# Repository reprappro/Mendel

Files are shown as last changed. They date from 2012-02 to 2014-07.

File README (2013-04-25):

This is repository the RepRapPro Tricolour and Mono Mendel.

Files for the latest extruder drive may be found here:

https://github.com/reprappro/Extruder-drive

Files for the original RepRapPro Mendel maybe found at the following address:

https://github.com/reprappro/Mendel/archive/Mendel-V1.0.zip

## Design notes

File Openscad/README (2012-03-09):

These OpenSCAD files have names that tell you how many copies to print.

Ones that end in readme make multiple objects - read the comments at their head
to find out what to print.

Ones that have neither ending are library files for the others.

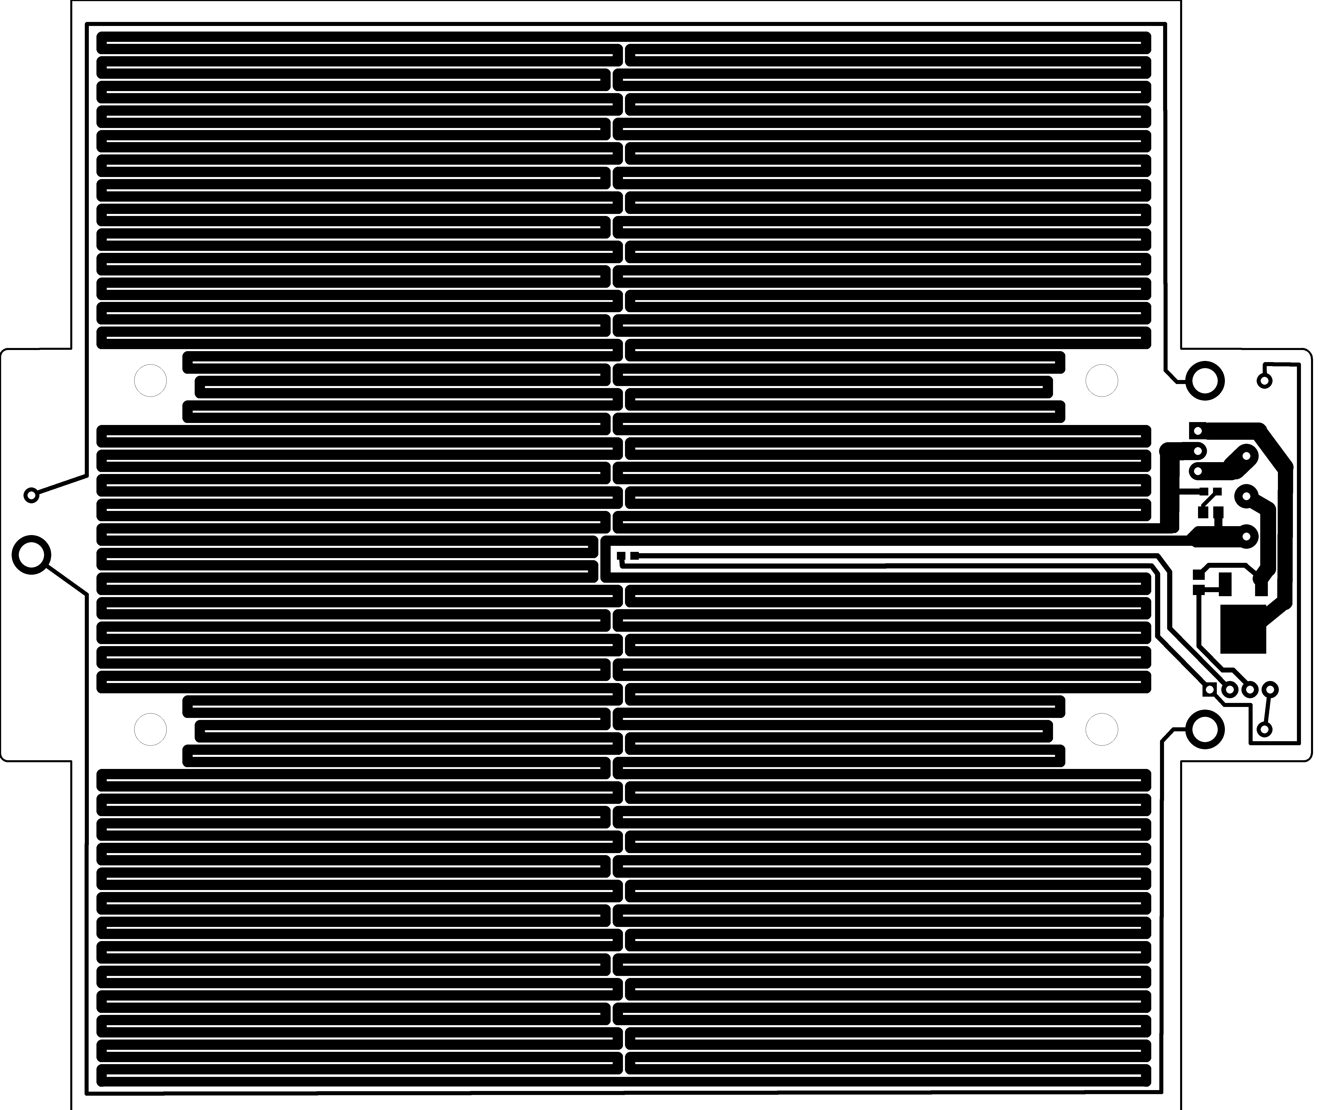
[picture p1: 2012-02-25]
gEDA/Heatbed/heatbed.png

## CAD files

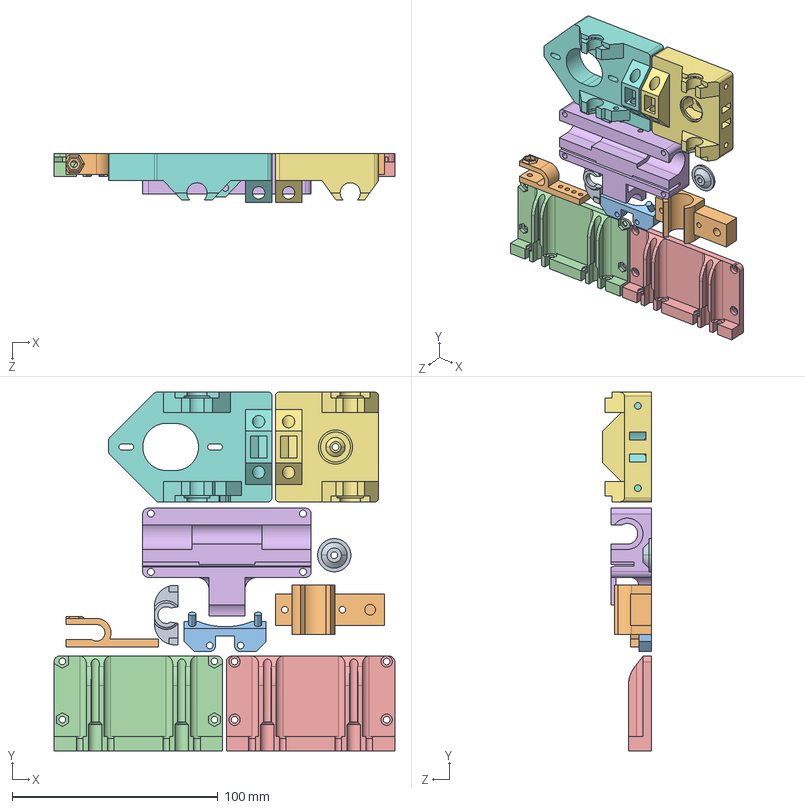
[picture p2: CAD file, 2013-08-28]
SW/Step/RP-assembly.STEP
165.8 x 174.6 x 23.6 mm
Belt Guide
EndStop-Holder
Fan Holder
nozzle-mount-front
nozzle-mount-rear
x-carriage
x-end-idler
x-end-motor
x-idler-cover
Y-Bearing-Holder

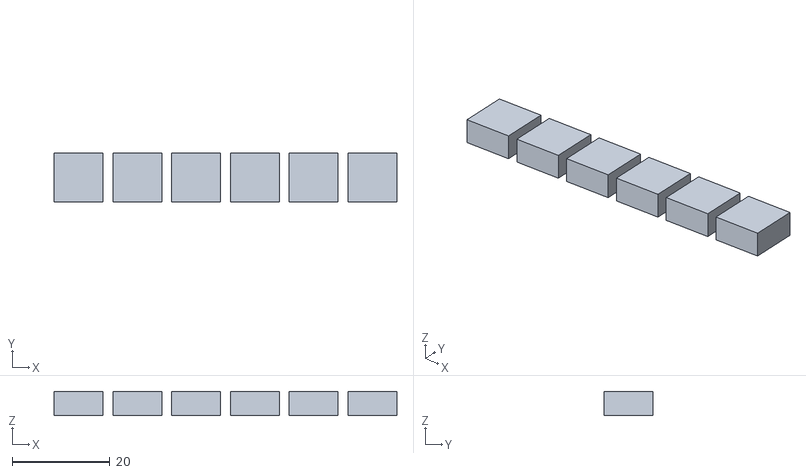
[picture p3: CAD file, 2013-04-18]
Multi-material/Calibration/Calibration 2/Mainextruder.STL
70.0 x 10.00 x 5.00

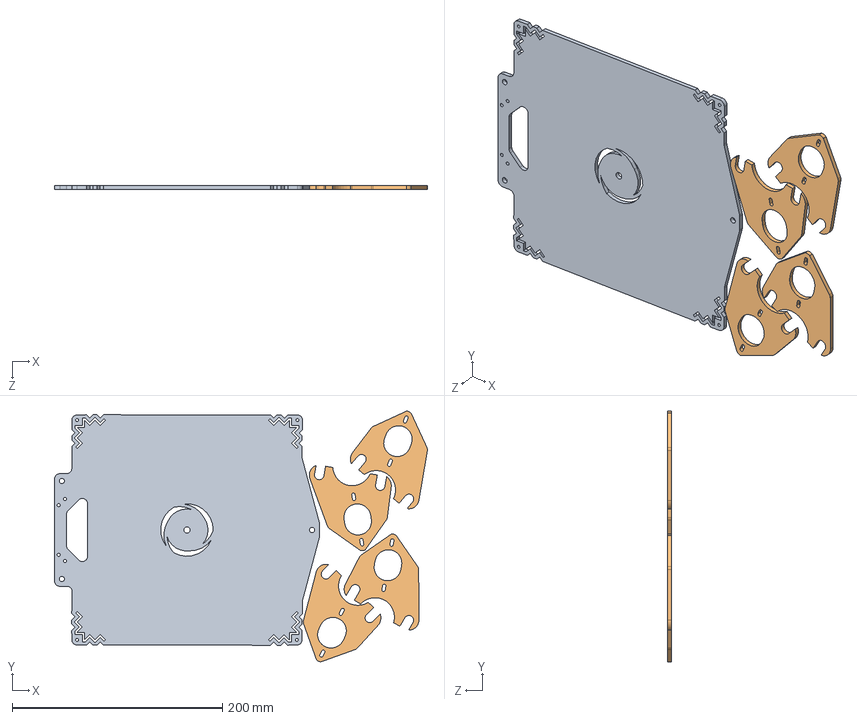
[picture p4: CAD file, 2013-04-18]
dxf/3mmSheet Layout.SLDASM
354.8 x 238.6 x 3.60 mm
Y-Motor-Bracket x 4

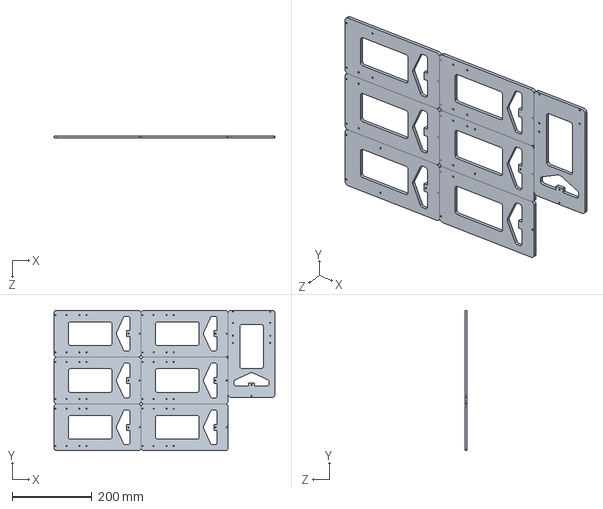
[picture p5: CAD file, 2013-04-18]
dxf/6mmSheet Layou.SLDASM
553.2 x 351.6 x 6.00 mm
Y-frog x 7

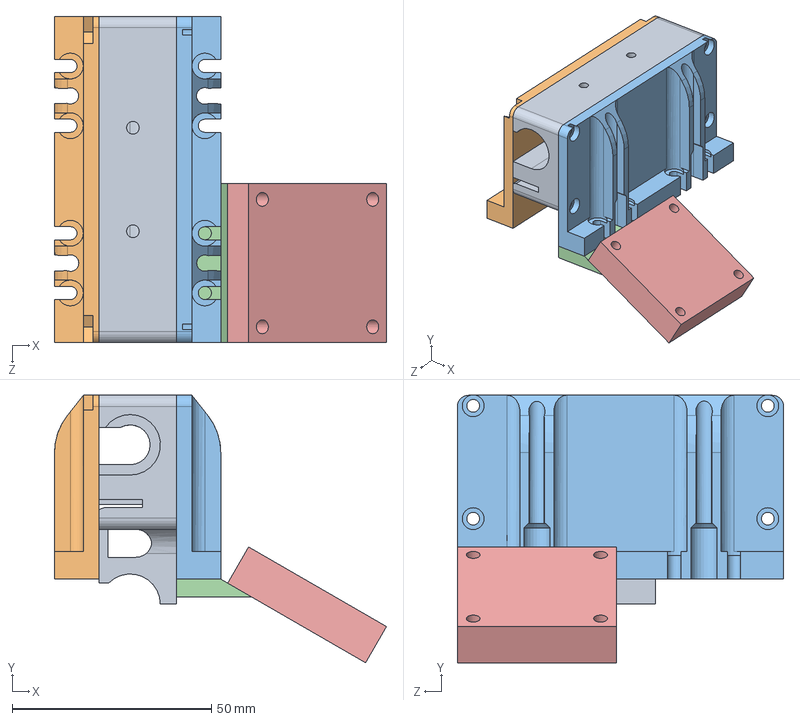
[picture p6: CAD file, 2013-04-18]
SW/Assem1.SLDASM
83.4 x 67.2 x 82.0 mm
x-carriage
nozzle-mount-front
nozzle-mount-rear
Fan Holder
Fan

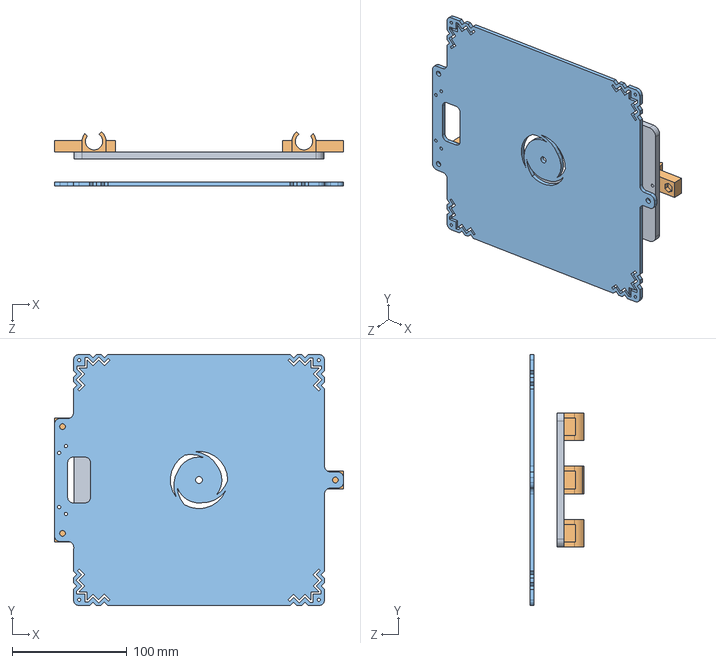
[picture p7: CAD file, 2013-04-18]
SW/Y Axis.SLDASM
252.0 x 219.3 x 47.4 mm
Y-frog
Y-Bearing-Holder x 3

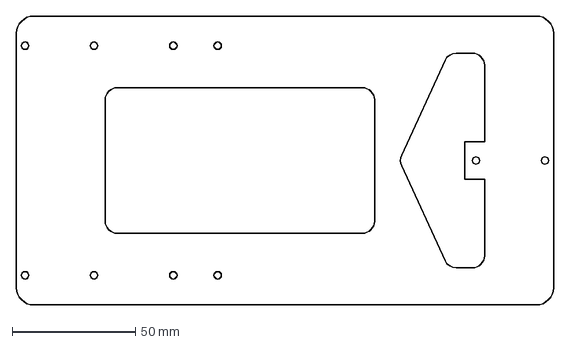
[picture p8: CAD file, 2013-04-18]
dxf/Y-frog.DXF
218.0 x 117.2 mm

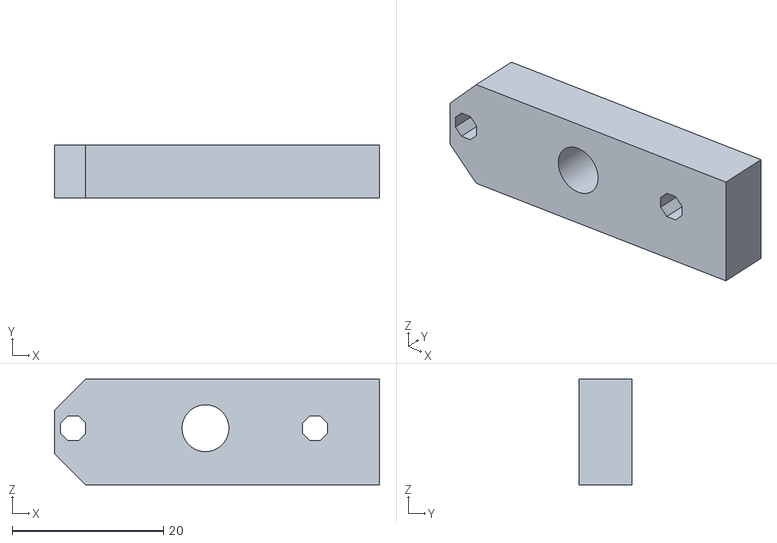
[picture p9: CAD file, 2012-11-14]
Mult-material/Openscad/extruder-drive-retainer-block.stl
43.0 x 7.00 x 14.0

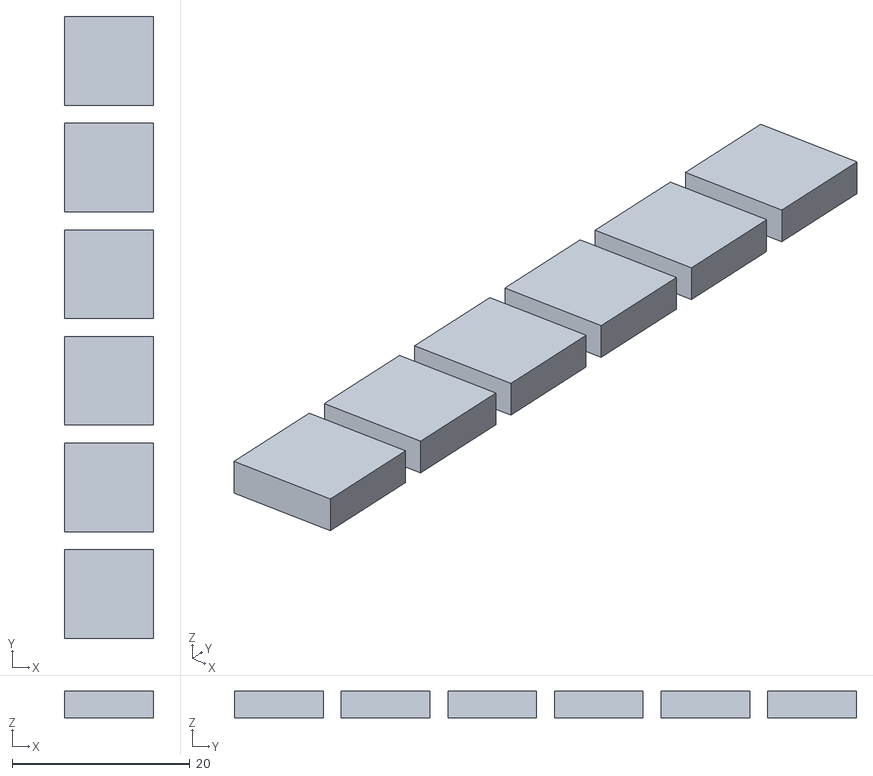
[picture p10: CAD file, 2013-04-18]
Multi-material/Calibration/Calibration 1/Extruder1.stl
10.0 x 70.0 x 3.00

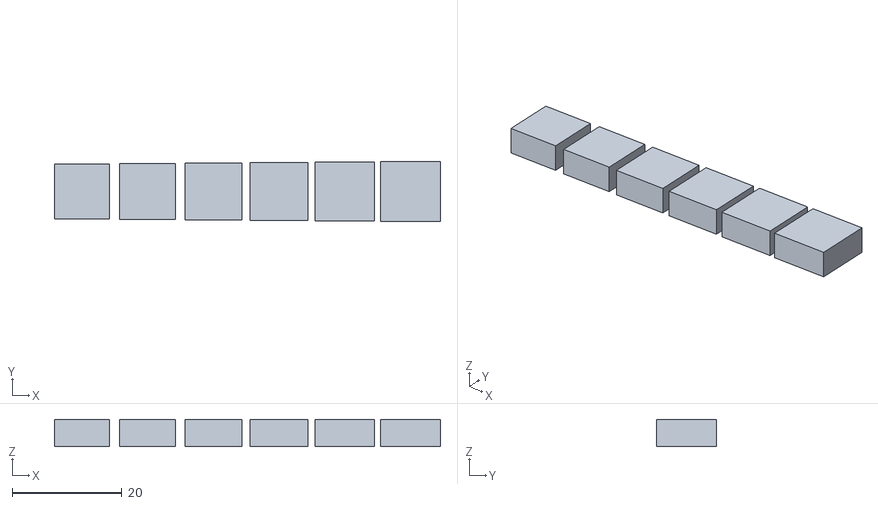
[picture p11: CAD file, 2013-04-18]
Multi-material/Calibration/Calibration 2/SecondaryExtruder.STL
70.5 x 11.0 x 5.00

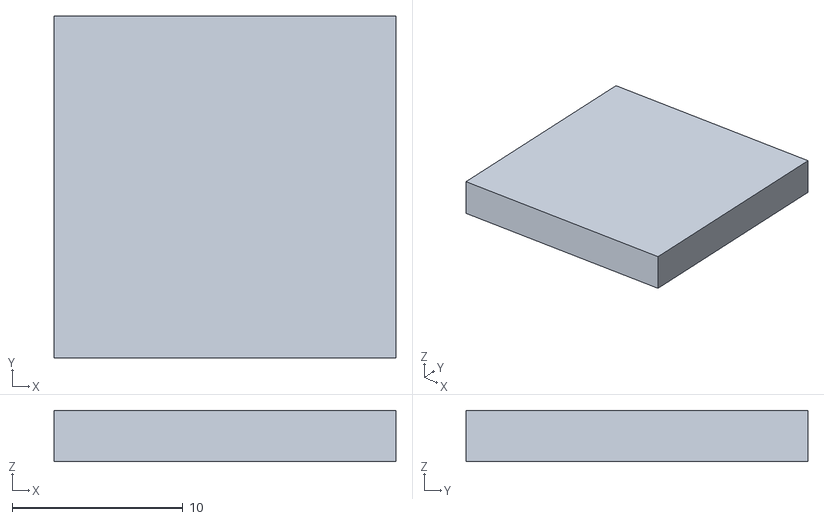
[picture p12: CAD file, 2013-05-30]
Multi-material/Calibration/Calibration 3/stacked-pair-bottom.stl
20.0 x 20.0 x 3.00

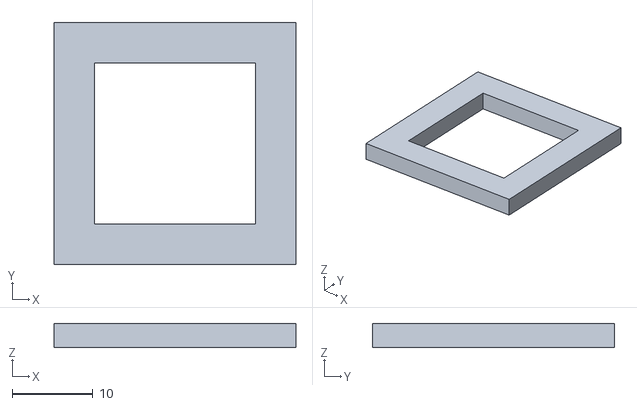
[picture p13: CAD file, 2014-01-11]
Multi-material/Calibration/e0.stl
30.0 x 30.0 x 3.00

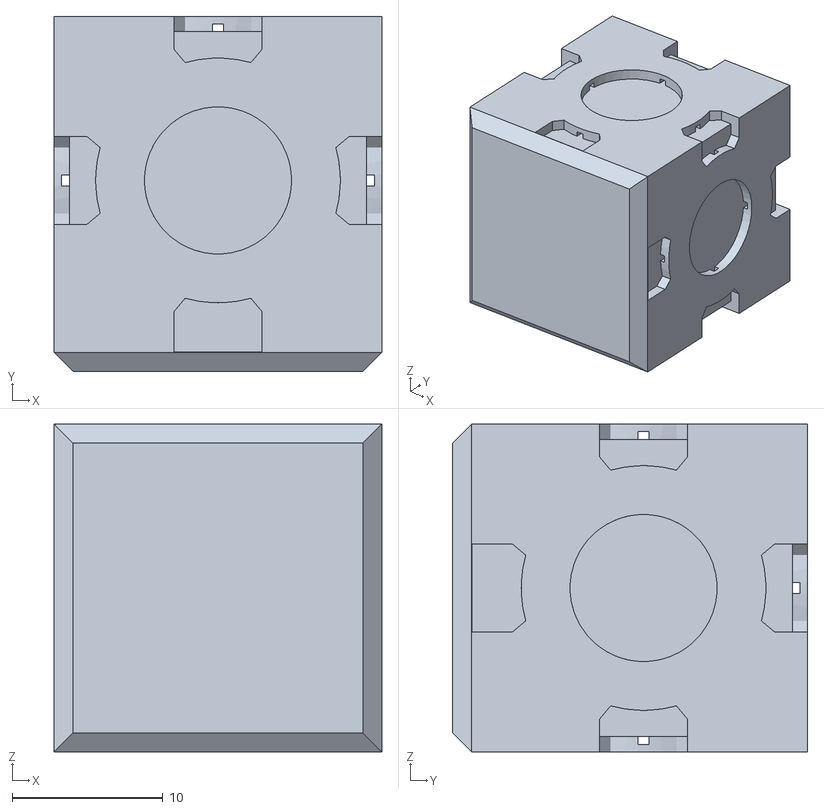
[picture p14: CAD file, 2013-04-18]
Multi-material/Sample Parts/Companion Cube/DarkGrey.stl
21.8 x 23.6 x 21.8

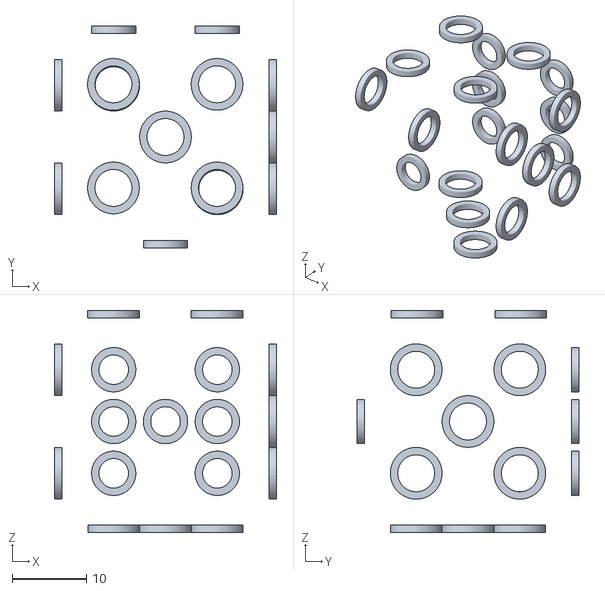
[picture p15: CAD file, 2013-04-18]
Multi-material/Sample Parts/Dice/Black.stl
30.0 x 30.0 x 30.0

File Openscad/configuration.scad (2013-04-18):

// PRUSA Mendel  
// Configuration file
// GNU GPL v2
// Josef Pra
// josefprusa@me.com
// prusadjs.cz
// http://www.reprap.org/wiki/Prusa_Mendel
// http://github.com/prusajr/PrusaMendel


// PLEASE SELECT ONE OF THE CONFIGURATIONS BELOW
// BY UN-COMMENTING IT


variant=0; //0 for metric
//variant=1; //1 for SAE
if(variant==0){
echo("variant: metric");
}else if(variant==1){
echo("variant: sae");
} else{
echo("WARNING: INVALID CONFIGURATION");
}




vars=[
//[m8_dia,m8_nut, m4_dia, m4_nut, m3_dia, m3_nut, bush_dia, mot_shaft, bush_rod, bush_outerdia, bush_length, m5_dia, m5_nut]
[8.4, 14.8, 4.3,8.1, 3.1, 6.5, 11, 5.3, 8, 16, 11, 5.3,9.3],//metric - M3 nut was 7; M3 was 4.4
[9,15.7,5.5,10.6,5.5,10.6,11.5,5.3,7.9375,16,11,5.6, 10]//SAE
];


//BUSHING TYPE Can generate three versions
// 1 - regular old ones
// 2 - helical ones
// 3 - holders for brass or any other bought bushings
bushing_type = 2;


//Round corner diameter
round_corner_diameter = 8;


//Thin wall size
layer_height = 0.4;
perimeter_width_over_thicknes = 1.6;
infill_widht_over_thickness = 1.55;
thin_wall = 2*(perimeter_width_over_thicknes*layer_height+infill_widht_over_thickness*layer_height);
if(thin_wall<2){
	echo("Check thin wall size, its below 2mm!");
}
echo(thin_wall);


//DO NOT TOUCH THIS SECTION!
m8_diameter = vars[variant][0];
m8_nut_diameter = vars[variant][1];
m4_diameter = vars[variant][2];
m4_nut_diameter = vars[variant][3];
m3_diameter = vars[variant][4];
m3_nut_diameter = vars[variant][5];
bushing_diameter = vars[variant][6];
motor_shaft=vars[variant][7];
bushing_rodsize = vars[variant][8];
bushing_outerDiameter = vars[variant][9];
bushing_lenght = vars[variant][10];
m5_diameter = vars[variant][11];
m5_nut_diameter = vars[variant][12];



// MINI-HUXLEY VERSION (TODO, just place holder)
// include <configuration-huxley.scad>


// MEGA VERSION (TODO, just place holder)
// include <configuration-mega.scad>

// Gap between the X rods

x_rod_centres=70;
y_rod_centres=183;
belt_width=6;
belt_clamp_centres=18;
ptfe_diameter=4;
z_slot_width=3.5;

vertex_x_rod_1=[11.013,59.912];
vertex_x_rod_2=[40.274,9.249,0];
vertex_x_rod_gap=sqrt((vertex_x_rod_1.x-vertex_x_rod_2.x)*(vertex_x_rod_1.x-vertex_x_rod_2.x) +(vertex_x_rod_1.y-vertex_x_rod_2.y)*(vertex_x_rod_1.y-vertex_x_rod_2.y) );

// Some basic functions, probably should be somewhere else
module roundcorner(diameter){
	difference(){
		cube(size = [diameter,diameter,99], center = false);
		translate(v = [diameter, diameter, 0]) cylinder(h = 100, r=diameter, center=true);
	}
}

include <functions.scad>

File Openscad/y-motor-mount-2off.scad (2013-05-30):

linear_extrude(file = "../dxf/Y-Motor-Bracket.DXF", layer = "0",
  height = 4, center = true, convexity = 10);

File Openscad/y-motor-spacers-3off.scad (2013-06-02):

// Print one of the objects generated when this is true, and one when it's false.
closed_spacer()
//open_spacer();

include <../configuration.scad> ;


cyl_height = 14 ;

module closed_spacer(){
	difference(){
		cylinder(h=cyl_height, r=7, $fn=6) ;
		cylinder(h=50,r=1.6,$fn=20) ;
		}
}



module open_spacer() {
				rotate([0,180,0])
				mirror([0,0,1])
				difference()	 {
									translate([-50.25,-20.35,0]) cylinder(h=cyl_height, r=8) ;
									union() {
										translate([-50.25,-20.35,-5]) cylinder(h=30,r=4.50,$fn=20) ;
										translate([-55.44,-17.35,10]) rotate(a=[0,0,-30]) cube(size = [12,9,30], center = true) ;
											}	

								}

} ;

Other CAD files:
SW/X-Axis.SLDASM
Mult-material/Print-mendel-mult-material/Individual-STLs/extruder-drive-retaining-block.stl
Multi-material/Sample Parts/Love Sculpture/Pink.STL
Multi-material/Sample Parts/Pro/R.stl
Openscad/z-motor-mount-2off.scad
Mult-material/Print-mendel-mult-material/Individual-STLs/bottom-arm.stl
Mult-material/Print-mendel-mult-material/Individual-STLs/drive-plate.stl
Mult-material/Print-mendel-mult-material/Individual-STLs/top-arm.stl
Multi-material/Calibration/Calibration 1/Calibration.ipt
Multi-material/Calibration/Calibration 1/Calibration.stl
Multi-material/Calibration/Calibration 1/Extruder2.stl
Multi-material/Calibration/Calibration 1/Extruder3.stl
Multi-material/Calibration/Calibration 1/OldVersions/Calibration.0003.ipt
Multi-material/Calibration/Calibration 2/Calibration.SLDPRT
Multi-material/Calibration/Calibration 3/stacked-pair-top.stl
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

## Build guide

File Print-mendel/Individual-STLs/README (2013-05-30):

The master files for the whole of RepRapPro Mendel are on Github here:

https://github.com/reprappro/Mendel

These are the all the printed parts except the extruder for a RepRapPro Mendel.

See: 

   http://reprappro.com/Tricolour_Mendel

and

   http://reprappro.com/Mono_Mendel

Both machines use the same files from this directory.  Each filename has the number-off
for that part that you need to print as part of its filename.  If you want a cooling fan on
your RepRap (this gives better quality, especially for prints with a small cross-sectional
area) print the optional fan-holder file too; otherwise leave it out.

The Y-motor-mount file is optional - you don't need it if you lasercut the Y motor mount, but
you can also print it.  Similarly with the Y-frog.  This is divided in two (A and B) for 
easier printing; bolt the two halves together with 4 M3x20mm cap screws.  (All the .dxf files for lasercutting are in the dxf directory in the Github repository.) 

In addition, for a Tricolour Mendel you will need three extruder drives from here:

https://github.com/reprappro/Extruder-drive

For a Mono Mendel, you need only one extruder drive.

For build instructions and lists of all the other hardware needed, see here:

http://reprappro.com/wiki/index.php/RepRapPro_Tricolour

RepRapPro sells hardware-only kits to go with the printed parts described above so that
you can print your own RepRap and then get all the additional hardware needed to build
and operate the complete machine from one place.  See the first two links above for details.

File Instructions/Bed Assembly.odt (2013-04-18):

Heated Bed

3 X M5 X 30 CSK

Laser Cut Insulator

PCB Bed Heater

Glass Build Plate

Foldback spring clips

13mm Springs

6X M5 Nuts

3 X M5 Nylock Nuts

10K Thermistor

Twin Ribbon Wire 1.1M

20A Wire 1.1M

3mm LED

1K Resistor

Aluminium Heat Spreder

<3 X16 countersunk screws x 4

3mm diameter heatshrink (black) 30mm

5.5mm dia heatshrink (Grey) 30mm

Cable Tie 1

4X M3 Washers

4x M3 Nylocks

# Goal

By the end of this step your RepRap machine should look like this:

(http://reprap.org/wiki/File:Reprappro-mendel-bed-finished.jpg)

And in addition it will have an aluminium plate on top of the red circuit board.

# [edit (http://reprap.org/mediawiki/index.php?title=RepRapPro_Mendel_heatbed_assembly&action=edit&section=2)]Tools

You will need the following tools:

1. M3 Allen key
2. Cross-head screwdriver
3. Multimeter
4. Soldering iron and solder

# [edit (http://reprap.org/mediawiki/index.php?title=RepRapPro_Mendel_heatbed_assembly&action=edit&section=3)]Parts

Hardware | Quantity | (http://reprap.org/wiki/File:Reprappro-mendel-bed-components.jpg) Click the image for a high-res version.
Lasercut insulator | 1
PCB bed heater | 1
Glass printing plate | 1
Foldback spring clips | 4
M3 x 40mm screws | 3
30mm springs | 3
M3 nuts | 13
M3 washers | 16
10K glass bead thermistor (arrowed; this is very very small) | 1
twin ribbon wire | 1.1m
20A wire | 1.1m
3mm LED | 1
1k resistor | 1
Aluminium heat spreader | 1
M3 x 10mm or 16mm countersunk screws* | 4
3mm dia. Heatshrink (usually black) | 30mm
5.5mm dia. Heatshrink (usually grey) | 30mm
Cable tie | 1

*Either works fine.

Get the twin ribbon wires by stripping them off the wider ribbon cable supplied with the kit. If that ribbon cable has a colored stripe down one side, strip the two wires furthest from it. If it has no coloured stripe, strip from one side, then put the remaining ribbon flat on the bench and run a felt-tipped marker down one side:

(http://reprap.org/wiki/File:Reprappro-mendel-bed-ribbon-marking.jpg)

This will make the wires in it easier to identify later. Set the wider ribbon aside for later use.

# [edit (http://reprap.org/mediawiki/index.php?title=RepRapPro_Mendel_heatbed_assembly&action=edit&section=4)]Step 1: Main assembly

(http://reprap.org/wiki/File:Reprappro-mendel-bed-sandwich-top.jpg)

Use the countersunk screws together with four nuts and washers to sandwich the heated bed PCB between the aluminium plate and the MDF insulator.

The zig-zag heater track on the PCB faces up towards the aluminium plate.

Make sure that the PCB solder terminals, the rectangular cut in the insulator, and the notch out of the aluminium plate all line up.

Take care not to break the lasercut springs in the corner of the insulator. (These are to allow for differential expansion.)

(http://reprap.org/wiki/File:Reprappro-mendel-bed-sandwich-bottom.jpg)

Here is a view of the underside. Use a pencil to mark + and - as shown. This will help with the wiring.

# [edit (http://reprap.org/mediawiki/index.php?title=RepRapPro_Mendel_heatbed_assembly&action=edit&section=5)]Step 2: Wiring

(http://reprap.org/wiki/File:Reprappro-mendel-bed-led-legs.jpg)

Bend the LED's legs and resistor legs as shown above and insert them from the MDF insulator side. The longer LED leg goes to the end marked +.

The LED and the resistor are in series, and the two of them together are in parallel with the main heater element - the zig-zag pattern of the PCB.

(http://reprap.org/wiki/File:Reprappro-mendel-bed-led-r-soldered.jpg)

Solder the LED and the resistor as shown on the aluminium plate side. You may find this easier if you prop the bed up on something clear of the bench.

Trim the wires flush with the top of the PCB using side cutters. Make sure that the connections do not project higher than the thickness of the aluminium plate, or they will foul the glass plate which will go on top of it.

Locate the 10K Glass Bead thermistor. This is very small and can get lost in the folds of the bag. It looks like this (M3 nut for size comparison):

(http://reprap.org/wiki/File:Reprappro-mendel-bed-thermistor.jpg)

(http://reprap.org/wiki/File:Reprappro-mendel-bed-thermistor-leads.jpg)

Solder the twin ribbon wires onto the thermistor as shown above. Stagger the connections. Use the insulation stripped from the short connection to insulate the thermistor wire.

Tin the ends of the wires, then tin the wires on the thermistor, then sweat them together.

(http://reprap.org/wiki/File:Reprappro-mendel-bed-thermistor-hs.jpg)

Insulate the joins with a length of heatshrink.

Strip the insulation from the other ends of the wires and use your meter to check the resistance. It should be about 10K ohms, though the exact value will depend on room temperature.

(http://reprap.org/wiki/File:Reprappro-mendel-bed-thermistor-fit-1.jpg)

Bend the thermistor at right angles and tape it to the bed. Make sure it goes through the hole in the insulator and the hole in the PCB and touches the aluminium plate. If you like you can add a little heatsink grease to improve the thermal contact between the thermistor and the plate.

(http://reprap.org/wiki/File:Reprappro-mendel-bed-thermistor-fit-2.jpg)

Pack the hole in the insulator with something fluffy: cotton wool or a bit of scrunched tissue both work well. Put tape over the hole. (The LED and resistor are the wrong way round in this picture - ignore them.)

Lead the wires to the edge of the bed where the two cable-grip holes are and tape them down. Use the holes on the side you marked -. Note the strain relief loop; don't run the wires straight.

(http://reprap.org/wiki/File:Reprappro-mendel-bed-power-wires-1.jpg)

Bare the ends of the high current wire. Put heatshrink on such that it covers only a couple of mm of the bare strands.

The picture shows one wire complete, the other ready to be wrapped.

(http://reprap.org/wiki/File:Reprappro-mendel-bed-power-wires-fitted.jpg)

Push the wires through the bed as shown and bend them flat against the tinned areas of the PCB (you may need to drill the holes out with a 3mm diameter drill first. Do this from the tinned side to get a clean hole). The wire with the black stripe goes to the side marked -. Solder the wires. Be generous with the solder (it's giving both mechanical strength and high current carrying capacity), but again make sure that the join is lower than the thickness of the aluminium plate.

Put the glass plate on the aluminium and make sure that none of the wires nor the LED stick out and foul it.

(http://reprap.org/wiki/File:Reprappro-mendel-bed-cable-tie.jpg)

Use the cable tie to attach the high-current wires and the thermistor wires. Again, note that the high-current wires are not pulled taught. They have a strain relief loop. Make sure they do not project too far on the MDF insulator side - if they do bend them gently flatter.

Pull the cable tie good and tight (but take care not to break the lasercut insulator), and then clip the excess off it.

# [edit (http://reprap.org/mediawiki/index.php?title=RepRapPro_Mendel_heatbed_assembly&action=edit&section=6)]Step 3: Attach to the machine

(http://reprap.org/wiki/File:Reprappro-mendel-bed-mounting-screw.jpg)

Put the three long screws through the mounting holes with washers under their heads.

Put the springs on. The sequence from the screw head goes:

1. Screw head
2. Washer
3. MDF insulator
4. Washer
5. Spring
6. Washer
7. Nut
8. Nut

(http://reprap.org/wiki/File:Reprappro-mendel-bed-mounted.jpg)

If you want a superb machine (of course you do), before you mount the bed put a little superglue on the heads of the screws that hold down the toothed-belt clamps, cut two rectangles of aluminium foil about 20 mm x 30 mm and glue these onto the screw heads. These will act as a heat shield, and will prevent the printed clamps from getting warm.

Note that we will shortly upgrade the design of the Y bearing mounts to move the hexagonal nut cavity to the top of them when when they are mounted in the machine. This will make bed adjustment easier.

Either way, pull the nuts into their hexagonal recesses in the printed bearing holders on the Y carriage with a shorter screw with a washer under its head. Take care that the nut and the hexagon are aligned.

Use the last three nuts and washers to mount the bed on the machine. If you have the newer variant the washers go underneath and you need to leave the lower nuts lose for the moment. If you have the older variant the washers go on top, and you need to do the nuts up on both sides of the printed Y bearing holder finger tight.

Adjust the screws to get the bed roughly level (measure the heights of the corners above the Y rods with digital callipers).

Tighten the nuts against the Y carriage to secure the bed.

Adjust the nuts above that set the spring compression so that the bed is held firmly against the screw heads, but can be pushed down with a finger.

Fit the glass plate using the four clips and check that the Y axis moves freely back and forth. Then take the glass off and put it in a safe place - you don't want to break it as you build the rest of the machine...

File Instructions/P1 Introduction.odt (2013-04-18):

RepRapPro Tricolour Mendel

  - Introduction

These pages are the complete instructions for building, commissioning and using the RepRapPro Ltd (http://reprappro.com/) version of RepRap Mendel.

Like all RepRap machines, RepRapPro Tricolour Mendel (http://reprappro.com/Mendel) is fully open-source. It is licenced under the GPL. All the design files and software are available from the RepRapPro Ltd Github (https://github.com/reprappro) repository. And it is here in the Thingiverse (http://www.thingiverse.com/thing:20968).

If you want to print the plastic parts for a RepRapPro Mendel, see this wiki page (http://reprap.org/wiki/How_to_Print_RepRapPro_Mendel).

RepRapPro Tricolour Mendel is based on the previous RepRap Pro Mendel with many alterations and additions. It was designed in order to further simplify assembly and to increase build volume when using multiple extruders.

These inital instructions document the assembly of a single material/colour “Mono” Mendel. It is recommended that even multicolour machines are initially assembled as Mono Mendels, before being extended to Tricolour machines after a commissioning.

General notes

Give yourself plenty of space and ensure your work area is clean. Dust and dirt are a 3D printer's worst enemy. All printed parts have been printed on various RepRap machines from suppliers within the RepRap community. Despite the fact that these machines are highly tuned RepRap 3D printers, some holes and features may need a little fettling to get the best performance from your machine. This is especially true for the Igus bushings used for the Z axis. There is a video how-to on fettling 3D printed parts here on Vimeo (http://vimeo.com/14492980).

Before you start the build, please ensure you have all the components as listed on the packing list included in the kit. If anything is missing, please contact us via email:

BEFORE YOU ATTEMPT TO ASSEMBLE ANY PART OF THE RepRapPro Mendel 3D PRINTER, PLEASE READ THESE BUILD INSTRUCTIONS FULLY AND ENSURE YOU UNDERSTAND THEM. Although all parts are covered by warranty, this will be invalidated by your not following these build instructions. If anything is unclear please get in contact with support prior to assembly in order to ensure no damage caused to your machine.

The RepRapPro Mendel is a robust RepRap machine once assembled; however it does require a certain amount of care during assembly. If in doubt, force is usually not the answer! There are many ways to get support and advice, see the Get Support section below.

If you can't see clearly from the pictures, they can be enlarged by clicking on them

Table of Contents

1. Frame assembly (http://reprap.org/wiki/RepRapPro_Mendel_frame_assembly)
2. Y axis assembly (http://reprap.org/wiki/RepRapPro_Mendel_y_axis_assembly)
3. X axis assembly (http://reprap.org/wiki/RepRapPro_Mendel_x_axis_assembly)
4. Z axis assembly (http://reprap.org/wiki/RepRapPro_Mendel_z_axis_assembly)
5. Heated bed assembly (http://reprap.org/wiki/RepRapPro_Mendel_heatbed_assembly)
6. Extruder drive assembly (http://reprap.org/wiki/RepRapPro_Mendel_extruder_drive_assembly)
7. Hot end assembly (http://reprap.org/wiki/RepRapPro_Mendel_hot_end_assembly)
8. Power supply (http://reprap.org/wiki/RepRapPro_Mendel_power_supply)
9. Wiring (http://reprap.org/wiki/RepRapPro_Mendel_wiring)
10. Commissioning (http://reprap.org/wiki/RepRapPro_Mendel_commissioning) & Software Installation
11. Printing (http://reprap.org/wiki/RepRapPro_Mendel_printing)
12. Multi-colour/multi-materials (http://reprap.org/wiki/RepRapPro_Multimaterials)
13. Maintenance (http://reprap.org/wiki/RepRapPro_Mendel_maintenance)
14. Troubleshooting (http://reprap.org/wiki/RepRapPro_Mendel_troubleshooting)
15. Improvements (http://reprap.org/wiki/RepRapPro_Mendel_improvements)

Get support

If you find you need help or advice with assembling, commissioning or using your RepRapPro Mendel 3d printer, you can use the following channels:

- Our Forum (http://www.emakershop.com/forum?vasthtmlaction=vforum&g=7.0). This sub-forum deals with the RepRapPro Mendel. Other sub-forums on the site deal with other eMaker and RepRapPro models.
- RepRapPro/eMaker channel on freenode irc (http://irc.netsplit.de/channels/?net=freenode&chat=emaker)

Tool List

Mechanical

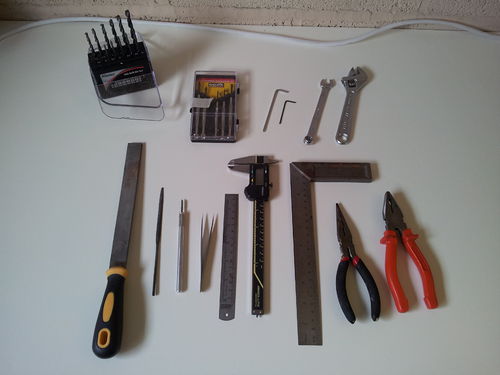
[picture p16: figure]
A description...

Tools required for the mechanical build of the RepRapPro Mendel 3D printer:

16. Drill bits including 2mm, 3mm, 6mm and 8mm
- Precision screwdriver set
- A set of metric allen keys including:
  - 2mm (M2.5 size)
  - 2.5mm (M3 size)
  - 4mm (M5 size)
- 13mm spanner (M8 nut)
- 8mm spanner (M5 nut)
- 5.5mm spanner (M3 nut)
- 5mm spanner (M2.5 nut)
- 15cm adjustable spanner
- File
- Half round needle file
- Craft knife
- Fine tweezers
- 300mm rule
- Vernier or digital calipers
- Square
- Fine nosed pliers
- Pliers
- Side cutters
- A small amount of superglue (for securing the hobbed insert)

Electrical

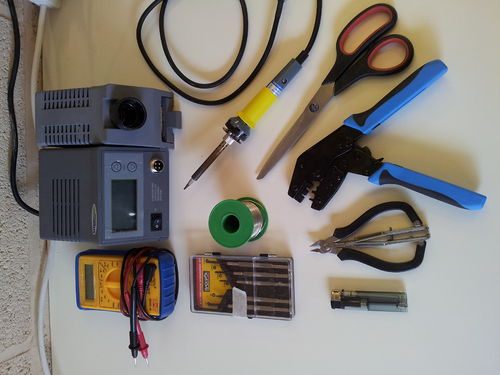
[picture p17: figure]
A description...

Tools required for the electrical build of the RepRapPro Mendel 3D printer:

- Digital Multimeter
- A fine-tipped soldering iron
- Precision screwdrivers
- Solder
- Hair dryer or cigarette lighter (or other heat source for heating heatshrink wire sleeving; the barrel of a soldering iron works OK)
- Wire strippers/cutters
- Ratchet crimp tool
- Molex crimp tool (such as the 63811-1000, you may also want the extraction tool 11-03-0044, Molexkits.com)
- Scissors

Next step

Frame assembly (http://reprap.org/wiki/RepRapPro_Mendel_frame_assembly)

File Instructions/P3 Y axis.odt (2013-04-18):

# Goal

By the end of this stage, your machine should look like this:

(http://reprap.org/wiki/File:Reprappro-mendel-y-axis-finished.jpg)

# Tools

You will need the following tools

- M8 (13mm) spanner
- Adjustable spanner
- M3 Allen key
- M3 spanner/nut runner
- Long-nosed pliers
- Side cutters

# Step 1: Y motor and mount

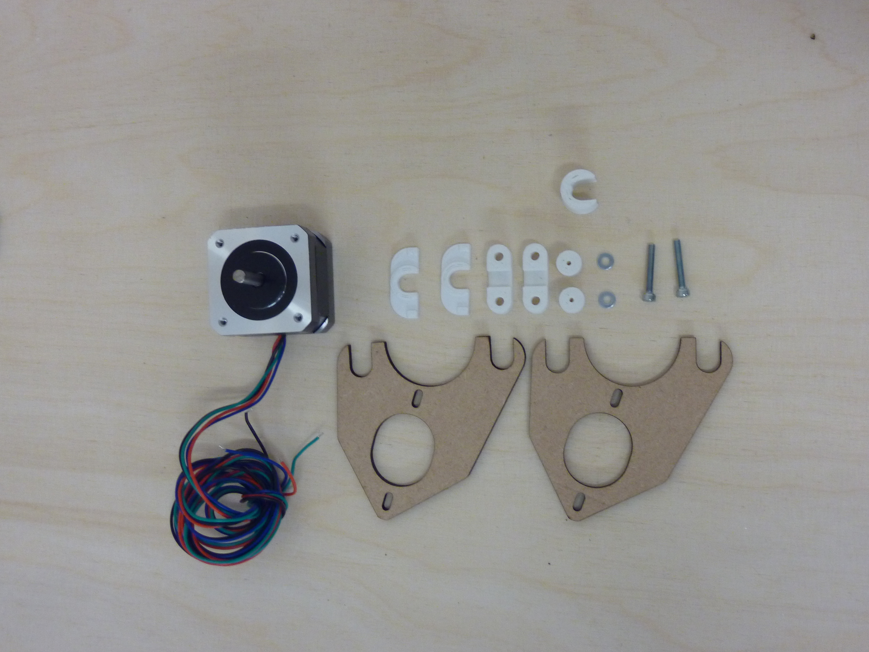
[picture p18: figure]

Item | Quantity
Lasercut Y Motor Mounts | 2
Printed Closed Spacer | 2
Nema 17 motor | 1
Printed Belt Guide | 2
M3 x 25mm screws | 2
M3 washers | 2
Printed MXL pulley | 1
Printed Open Spacer | 1

In addition to the above, a printed MXL pulley is also required:

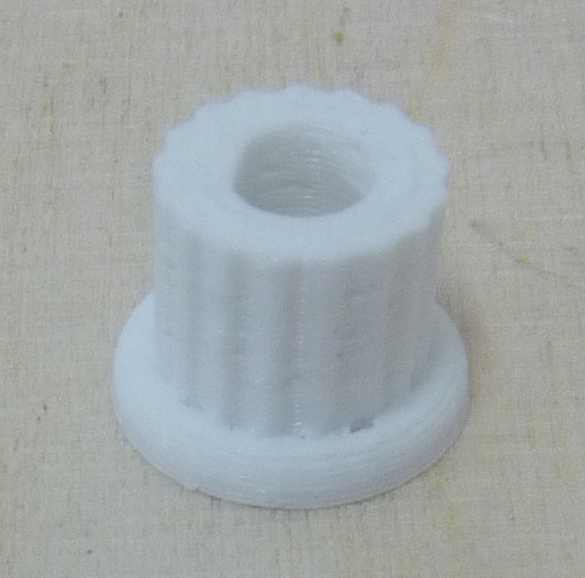
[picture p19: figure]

These simply push-fit onto the motor shaft and don't need a set screw

Use the two short screws to attach the motor to the half of its mount with the projections Insert one of the M3 cap screws and a washer through one of the slots in the motor mount, through one of the closed spacers and then finally through one of the slots of the other motor mount. Repeat this for the remaining slot. Finally attach this assembly to the Nema 17 motor. The wire orientation should be facing the circular cut out of Y motor mount as shown.

(http://reprap.org/wiki/File:Reprappro-mendel-y-motor-mount-1.jpg)

The wires come out of the bottom side of the motor in this picture.

(http://reprap.org/wiki/File:Reprappro-mendel-y-motor-mount-2.jpg)

Use the remaining screws, washers and nut to attach the other half of the mount cage. There is a recess for the nut, which should be a tight fit. Take care when tightening to pull the nut into its recess that the hexagon of the nut is aligned with the hexagonal recess.

# Step: 2 The Y frog

(http://reprap.org/wiki/File:Reprappro-mendel-y-frog-parts.jpg)
Item | Quantity
Lasercut frog | 1
LM8UU bearings | 3
Printed bearing holders | 3
Printed belt clamps | 2
M3 x 20mm screws | 10
M3 nylock nut | 10
M3 washers | 20

Attach the bearing holders to the lasercut part with 20mm cap screws, nylock nuts and washers (2 washers per screw, one on each side). Don't tighten the nuts:

(http://reprap.org/wiki/File:Reprappro-mendel-y-frog-1.jpg)

Push the bearings into the bearing holders from the side as shown on the right. Do not try to clip them in from on top. The bearings should be a snug fit. But if they are a bit lose, simply wrap a little Kapton tape two or three times round the lose bearing. Get it flat without wrinkles or bubbles.

Attach the belt holders:

(http://reprap.org/wiki/File:Reprappro-mendel-y-frog-2.jpg)

(http://reprap.org/wiki/File:Reprappro-mendel-y-frog-3.jpg)

Fit the nylock nut in the hexagonal hole in the tensioner, and loosely put the remaining screw in it. This screw will tension the belt by pushing on it.

Now to fit the frog to the machine:

(http://reprap.org/wiki/File:Reprappro-mendel-y-frog-fitted.jpg)

With the front of the machine facing you, slacken the right-hand nuts only that hold the U clamps with the smooth Y rods. (If you leave the left-hand nuts alone you will be able to re-tighten the rods in exactly the same place - so make sure they don't turn.)

Slide the rods towards the back of the machine. Slide the Y frog over them, using a gentle twisting motion to insert the rods into bearings while watching the opposite end of each bearing to make sure none of its balls get pushed out of their tracks. If they do, they can be reseated by pressing them back into the track with the tip of a chopstick. As a precaution, cover the area under the frame with a tissue to catch any balls that might fall out.

Replace the rods in their U clamps and re-tighten the right-hand nuts on those.

Tighten the M3 screws and nuts that attach the bearing holders to the frog.

Check that the frog slides completely freely back and forth. If it is tight at one end and lose at the other, then the rods aren't parallel. If it is tight at both ends and lose in the middle, then the rods are too close or too far apart. In both cases, measure the rod gap (which should be 175 mm from before - remember the lasercut measuring template) at both ends and in the middle, and get things right by adjusting the right-hand rod only.

# Step 3: The Y belt

(http://reprap.org/wiki/File:Reprappro-mendel-y-belt-parts.jpg)
Item | Quantity
Toothed belt | 900mm
Printed XY endstop holder | 1
microswitch | 1
M2.5x16mm screws | 2
M2.5 washers | 4
M2.5 nuts | 2
M3x20mm screw | 1
M3 washers | 2
M3 nuts | 1

Note that the X and Y axis endstop holders are identical, and you want one of those. The Z endstop holder has a longer leg.

Use the full length of toothed belt with your kit to fit this together. You will cut it to the right length when you have finished this step.

Bend the lead on the microswitch as shown in the picture above.

Fit the Y motor and mount:

(http://reprap.org/wiki/File:Reprappro-mendel-y-motor-fitted.jpg)

Adjust its position so that the middle of the bearing is opposite the belt-tensioning screw on the frog. You will find that for this and the idler below you can put your eye level with the frog and line up the middle of the bearings with the belt guide on the frog.

Tighten the four M8 nuts that hold the Y motor mount, taking care that the distance from the left-hand top and bottom nuts to the corresponding nuts on the frame vertices are the same.

Tighten the Y-belt idler:

(http://reprap.org/wiki/File:Reprappro-mendel-y-belt-idler.jpg)

Line the bearing up to match the belt clamp on the frog.

If you have done everything right so far, the belt tensioner on the frog should be towards the back of the machine.

Put one end of the belt between the bottom clamp on the tensioner and the tensioner part with the nylock nut in. Have the free length of the belt pointing towards the front of the machine. Position the belt so that its teeth lock with the indentations in the tensioner. You should be able to feel this as you move the belt.

Run the belt up through the hole in the frog, and fold it back in the groove in the belt guide. Get the belt square and central in the guide and clamp, then tighten the M3 screws and nuts that retain it. These need to be tight, but not so tight that they bend the clamp.

Run the belt over the bearing above the motor, round the motor's drive pulley, under the frog to the front of the machine, over the idler pulley, and back to the clamp on the front of the frog.

Thread the belt through the front clamp, get everything square, and pull the belt so there is no slack. It doesn't need to be taught.

Tighten the clamp.

Check the toothed drive pulley on the motor - it needs to be positioned so that the belt runs over the centre of the bearing. Slacken its set screw and move it if need be.

Cut off any spare belt with sidecutters - leave about 20mm free sticking out of the far side of the clamp.

Set the belt tension with the tensioning screw. The belt needs to be taught, but no so taught that it impedes the turning of the motor. Be gentle...

Check that the frog still moves freely front and back in the machine - there should be a certain resistance from the magnets in the motor, that is all.

Also check that the belt runs true. It should not tend to move from side to side more than 1mm or so. If it drifts (and especially if it rubs against edges and so becomes hard to move) then adjust the front bearing left or right to get the belt running square over that. You can move the motor left and right too, but it is often more effective to slacken its nuts and to tilt it very slightly relative to the threaded bars by not having the bars at the very bottom of the U-shaped slots in the motor's carrying frame. Then re-tighten the nuts.

Cut the off the excess belt - the remainder will be used to make the X axis. Leave 10mm or so sticking out of the clamps at either end.

Finally, attach the endstop microswitch to the h-shaped printed bracket with the M2.5 screws, washers and nuts. Attach the bracket to the frame at the back beside the motor:

(http://reprap.org/wiki/File:Reprappro-mendel-y-endstop-fitted.jpg)

Use the M3 screw, two washers, and nut to secure it. Before tightening these, make sure that the frog hits the button on the switch at the end of its travel.

# Next stage

Assemble the X axis. (http://reprap.org/wiki/RepRapPro_Mendel_x_axis_assembly)

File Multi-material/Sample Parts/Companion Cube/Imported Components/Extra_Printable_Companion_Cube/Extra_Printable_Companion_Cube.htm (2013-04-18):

Autodesk Inventor Translation Report | Thursday, February 14, 2013 (7:08 PM)

Source File: | Y:\Mult-material\Sample Parts\Companion Cube\Extra_Printable_Companion_Cube.SLDPRT
Translator Type: | SolidWorks | Sending System: | SolidWorks unknown
Author: | | Translation Time: | 00:00:10

Options
Import Type: | N/A
Entity Types to Import: | Solids, Surfaces, Wires
Import into Repair Environment: | Yes
Import Assembly as Single Part: | No
Create Surfaces As: | Single Composite Feature
Import Multiple Solid Parts as Assembly: | N/A
Units:
Check Parts during Load: | No
Auto Stitch: | No
Enable Advanced Healing: | N/A

## Components

The following table lists the parts and assemblies created in Inventor:

+/- | Name | Inventor File | Status
[+] [-] | Extra_Printable_Companion_Cube | Y:\Mult-material\Sample Parts\Companion Cube\Imported Components\Extra_Printable_Companion_Cube\Extra_Printable_Companion_Cube.ipt | Error

Severity | Entity Id | Message
Error | 0 | Translation failed. This version is not supported.

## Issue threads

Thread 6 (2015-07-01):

What part provides the L shaped bracket that goes from the X carriage to the 'hot end'

pkTux, 2015-07-01:
Looked through all the STL files & cannot establish if I am missing something, or just not familiar with the jargon.
i have all the X axis parts like idler, motor,  X carriage, ready to print.

RRP-support, 2015-07-01:
This is an automated reply to your message "[Mendel] What part provides the L shaped bracket that goes from the X
 carriage to the 'hot end' (#6)" sent to support@reprappro.com.

Dear Phillip Kenyon <notifications@github.com>

Thank you for your email. We endeavour to answer all emails within 24 hours. It may take longer during busy times, and holiday periods. We process all customer queries on a first come first served basis, during our office hours which are 9am to 5pm GMT Mon-Fri.

Other support channels are available. Please refer to the relevant troubleshooting guide for your machine:

Ormerod 2: https://reprappro.com/documentation/ormerod-2/troubleshooting/
Ormerod: https://reprappro.com/documentation/ormerod/troubleshooting/

Huxley Duo: https://reprappro.com/documentation/huxley-duo/troubleshooting/
Huxley: https://reprappro.com/documentation/huxley/troubleshooting/

Mono and Tricolour Mendel: https://reprappro.com/documentation/mendel-tricolour/troubleshooting/

Support is also available from other owners of RepRapPro and other 3D printers, either through the RepRap Forums: https://forums.reprap.org or through IRC which can be accessed from here: https://reprappro.com/support-channel/ (works on Chrome, not Firefox).

Best regards,

RepRapPro Support Team.

RRP-support, 2015-07-02:
Hi
There's a list of printed parts required, related to the part number, on the first page of the instructions. See: https://reprappro.com/documentation/mendel-3/#Printing_parts_for_Mendel_3
Ian
RepRapPro tech support

pkTux, 2015-07-02:
are you saying the part named ' nozzle mount' is what i need to reprint?

On Thu, Jul 2, 2015 at 5:09 AM, RRP-support <notifications@github.com>
wrote:

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

RRP-support, 2015-07-02:
This is an automated reply to your message "Re: [Mendel] What part provides the L shaped bracket that goes from
 the X carriage to the 'hot end' (#6)" sent to support@reprappro.com.

Dear Phillip Kenyon <notifications@github.com>

Thank you for your email. We endeavour to answer all emails within 24 hours. It may take longer during busy times, and holiday periods. We process all customer queries on a first come first served basis, during our office hours which are 9am to 5pm GMT Mon-Fri.

Other support channels are available. Please refer to the relevant troubleshooting guide for your machine:

Ormerod 2: https://reprappro.com/documentation/ormerod-2/troubleshooting/
Ormerod: https://reprappro.com/documentation/ormerod/troubleshooting/

Huxley Duo: https://reprappro.com/documentation/huxley-duo/troubleshooting/
Huxley: https://reprappro.com/documentation/huxley/troubleshooting/

Mono and Tricolour Mendel: https://reprappro.com/documentation/mendel-tricolour/troubleshooting/

Support is also available from other owners of RepRapPro and other 3D printers, either through the RepRap Forums: https://forums.reprap.org or through IRC which can be accessed from here: https://reprappro.com/support-channel/ (works on Chrome, not Firefox).

Best regards,

RepRapPro Support Team.

RRP-support, 2015-07-02:
I don't know what you have printed, or what you want to print. I assumed you meant the X axis parts. The nozzle mount was missing from your initial list. The list I linked above shows all the parts you need, and that are used in building the Mendel. Click on the link in the table and you'll get a preview of the STL file. If you are looking for specific parts, look at that section of the instructions, write down the parts and/or part numbers, and refer to the list.
Ian
RepRapPro tech support

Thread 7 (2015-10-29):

x-end-idler-1off.stl Missing Proximity Endstop

kipbits, 2015-10-29:
Hello, I've been ironing out some kinks with my printer recently, and wanted to make an alteration to the way my x axis is mounted on the z axis(to help it slide better). I noticed though, that the STL file for the x-end-idler does not seem to be the same version as what i have on my Mendel_3. I'm wondering if there is a newer file? and if it is available?

Thanks,
kipbits

RRP-support, 2015-10-29:
This is an automated reply to your message "[Mendel] x-end-idler-1off.stl Missing Proximity Endstop (#7)" sent to support@reprappro.com.

Dear kipbits <notifications@github.com>

Thank you for your email. We endeavour to answer all emails within 24 hours. It may take longer during busy times, and holiday periods. We process all customer queries on a first come first served basis, during our office hours which are 9am to 5pm GMT Mon-Fri.

Other support channels are available. Please refer to the relevant troubleshooting guide for your machine:

Ormerod 2: https://reprappro.com/documentation/ormerod-2/troubleshooting/
Ormerod: https://reprappro.com/documentation/ormerod/troubleshooting/

Huxley Duo: https://reprappro.com/documentation/huxley-duo/troubleshooting/
Huxley: https://reprappro.com/documentation/huxley/troubleshooting/

Mono and Tricolour Mendel: https://reprappro.com/documentation/mendel-tricolour/troubleshooting/

Support is also available from other owners of RepRapPro and other 3D printers, either through the RepRap Forums: https://forums.reprap.org or through IRC which can be accessed from here: https://reprappro.com/support-channel/ (works on Chrome, not Firefox).

Best regards,

RepRapPro Support Team.

RRP-support, 2015-10-29:
Hi kipbits
You're looking at the older Mendel repository, for Mendel '2'. See this repo: https://github.com/reprappro/Mendel-3
Or follow the links from the instructions, here: https://reprappro.com/documentation/mendel-3/#Printing_parts_for_Mendel_3
Ian
RepRapPro tech support

kipbits, 2015-10-30:
thanks , knew i was missing something

RRP-support, 2015-10-30:
This is an automated reply to your message "Re: [Mendel] x-end-idler-1off.stl Missing Proximity Endstop (#7)" sent to support@reprappro.com.

Dear kipbits <notifications@github.com>

Thank you for your email. We endeavour to answer all emails within 24 hours. It may take longer during busy times, and holiday periods. We process all customer queries on a first come first served basis, during our office hours which are 9am to 5pm GMT Mon-Fri.

Other support channels are available. Please refer to the relevant troubleshooting guide for your machine:

Ormerod 2: https://reprappro.com/documentation/ormerod-2/troubleshooting/
Ormerod: https://reprappro.com/documentation/ormerod/troubleshooting/

Huxley Duo: https://reprappro.com/documentation/huxley-duo/troubleshooting/
Huxley: https://reprappro.com/documentation/huxley/troubleshooting/

Mono and Tricolour Mendel: https://reprappro.com/documentation/mendel-tricolour/troubleshooting/

Support is also available from other owners of RepRapPro and other 3D printers, either through the RepRap Forums: https://forums.reprap.org or through IRC which can be accessed from here: https://reprappro.com/support-channel/ (works on Chrome, not Firefox).

Best regards,

RepRapPro Support Team.

Closed 2015-10-30.

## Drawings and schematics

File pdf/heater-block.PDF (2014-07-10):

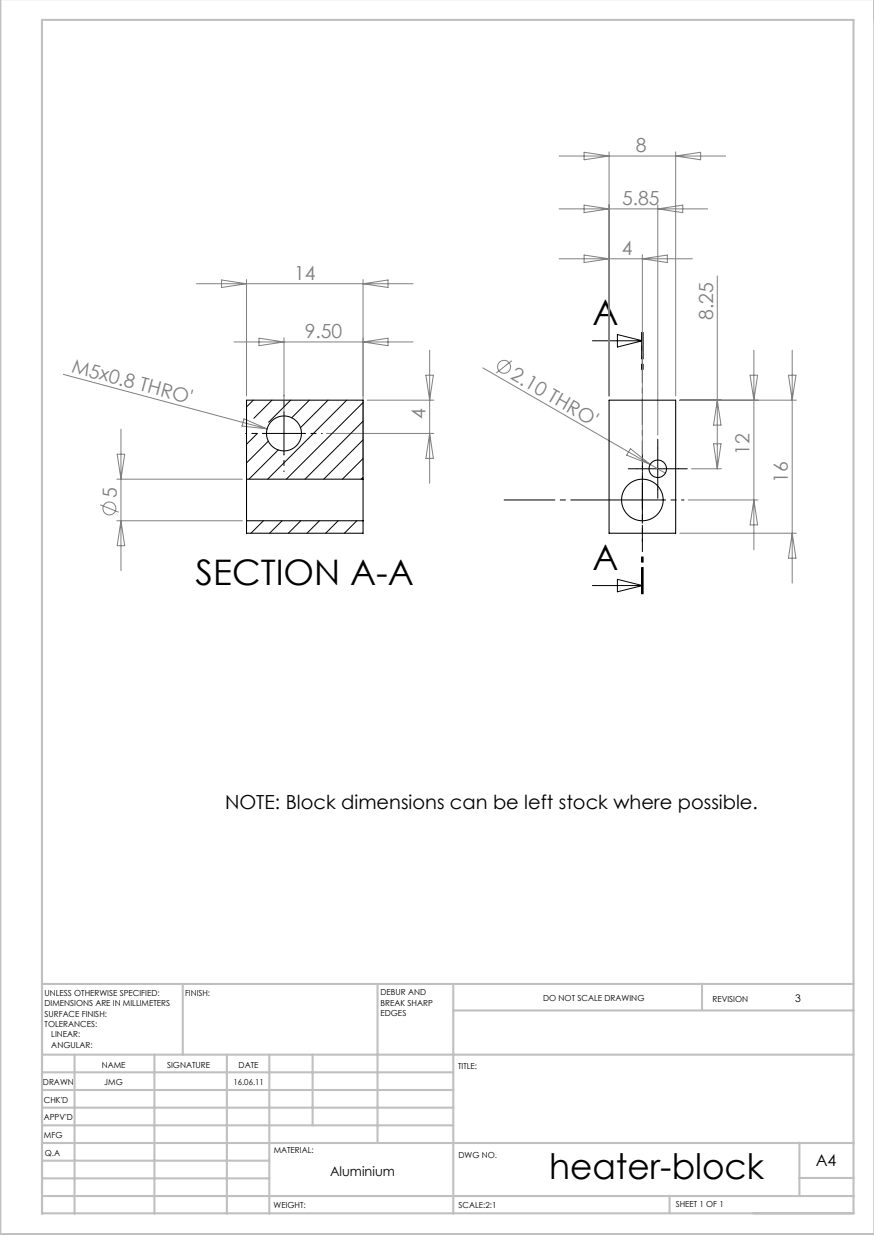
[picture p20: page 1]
2.10 THRO'; M5x0.8 THRO'; SECTION A-A; SCALE:2:1; SHEET 1 OF 1; DO NOT SCALE DRAWING; REVISION; DEBUR AND BREAK SHARP; UNLESS OTHERWISE SPECIFIED:; FINISH:

NOTE: Block dimensions can be left stock where possible.

DIMENSIONS ARE IN MILLIMETERS
SURFACE FINISH:
TOLERANCES:
LINEAR:
ANGULAR:

NAME | SIGNATURE | DATE | | | | TITLE:
Q.A | | | | MATERIAL: Aluminium | heater-block DWG NO. | A4

DRAWN | JMG | | 16.06.11
CHK'D
APPV'D
MFG

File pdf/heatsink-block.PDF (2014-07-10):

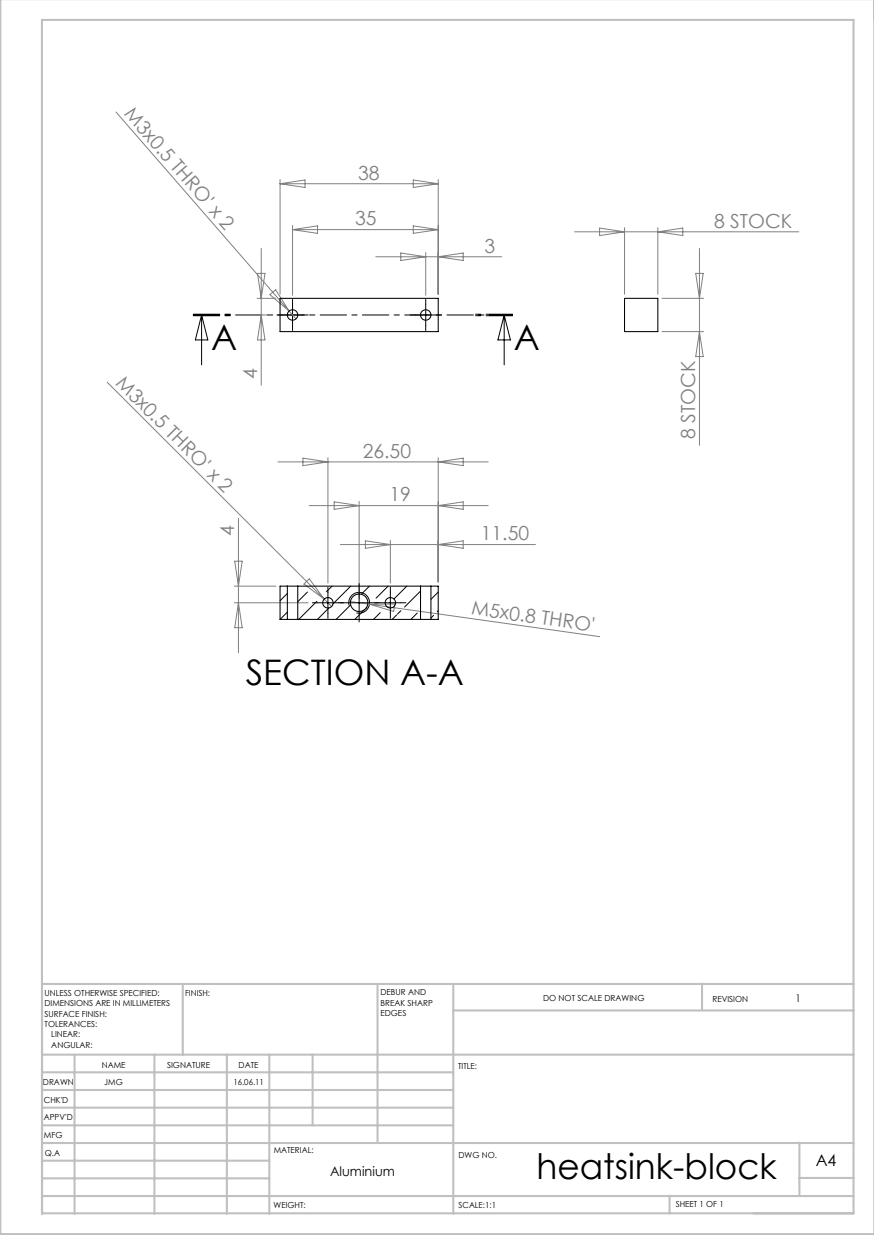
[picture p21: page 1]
M3x0.5 THRO' x 2; 8 STOCK; M5x0.8 THRO'; SECTION A-A; SCALE:1:1; SHEET 1 OF 1; DO NOT SCALE DRAWING; REVISION; DEBUR AND BREAK SHARP; UNLESS OTHERWISE SPECIFIED:; FINISH:

DIMENSIONS ARE IN MILLIMETERS
SURFACE FINISH:
TOLERANCES:
LINEAR:
ANGULAR:

NAME | SIGNATURE | DATE | | | | TITLE:
Q.A | | | | MATERIAL: Aluminium | heatsink-block DWG NO. | A4

DRAWN | JMG | | 16.06.11
CHK'D
APPV'D
MFG

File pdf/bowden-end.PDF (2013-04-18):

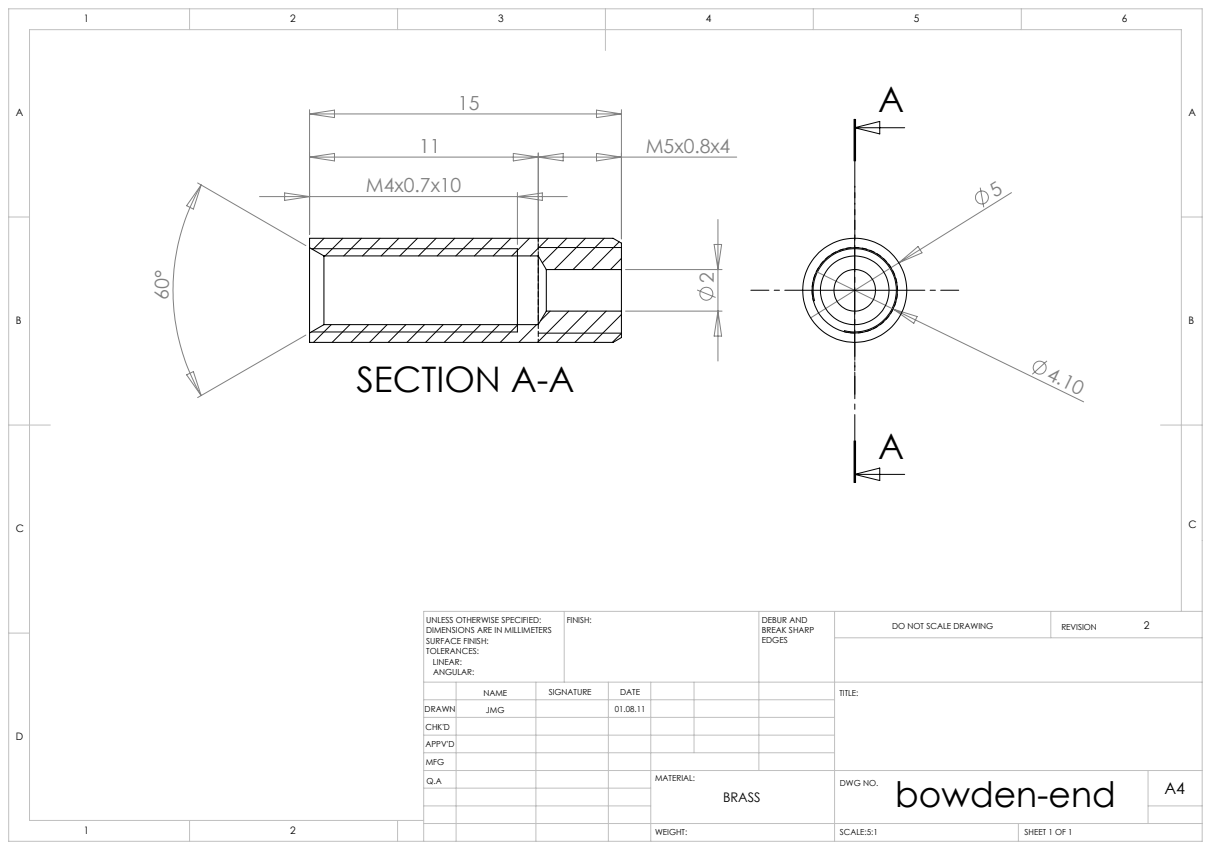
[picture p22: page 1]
SECTION A-A; FINISH:; DEBUR AND; BREAK SHARP; DO NOT SCALE DRAWING; REVISION; SCALE:5:1; SHEET 1 OF 1

UNLESS OTHERWISE SPECIFIED:
DIMENSIONS ARE IN MILLIMETERS
SURFACE FINISH:
TOLERANCES:
LINEAR:
ANGULAR:

NAME | SIGNATURE | DATE | | | | TITLE:

DRAWN | JMG | | 01.08.11
CHK'D
APPV'D
MFG
Q.A | | | | MATERIAL: BRASS | bowden-end DWG NO. | A4

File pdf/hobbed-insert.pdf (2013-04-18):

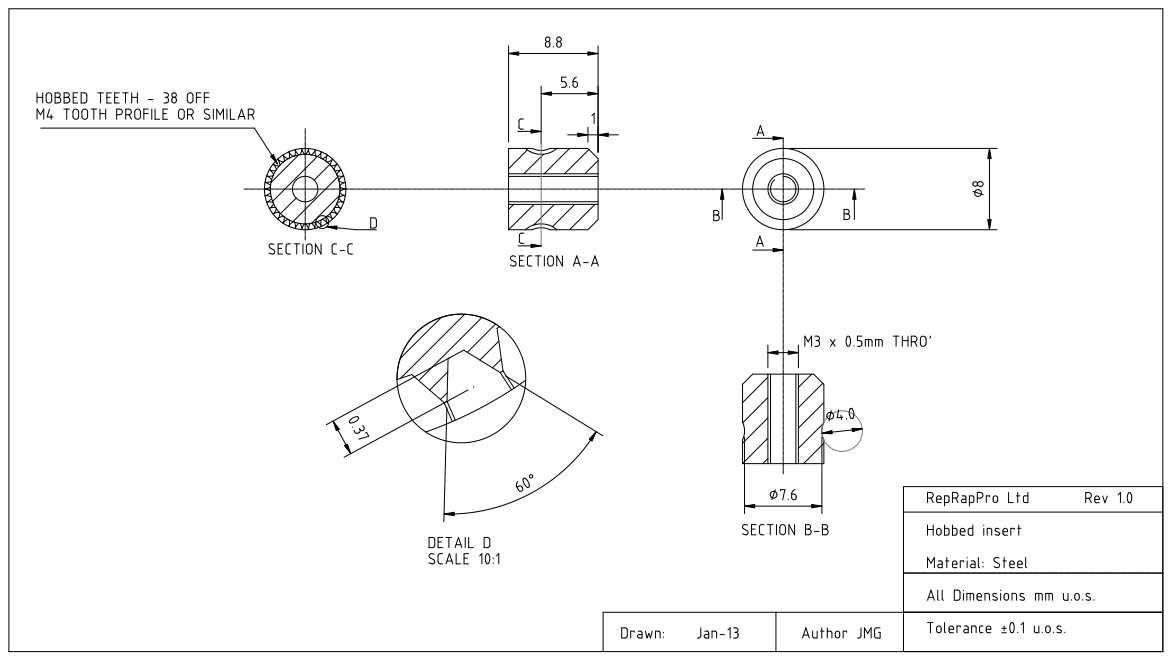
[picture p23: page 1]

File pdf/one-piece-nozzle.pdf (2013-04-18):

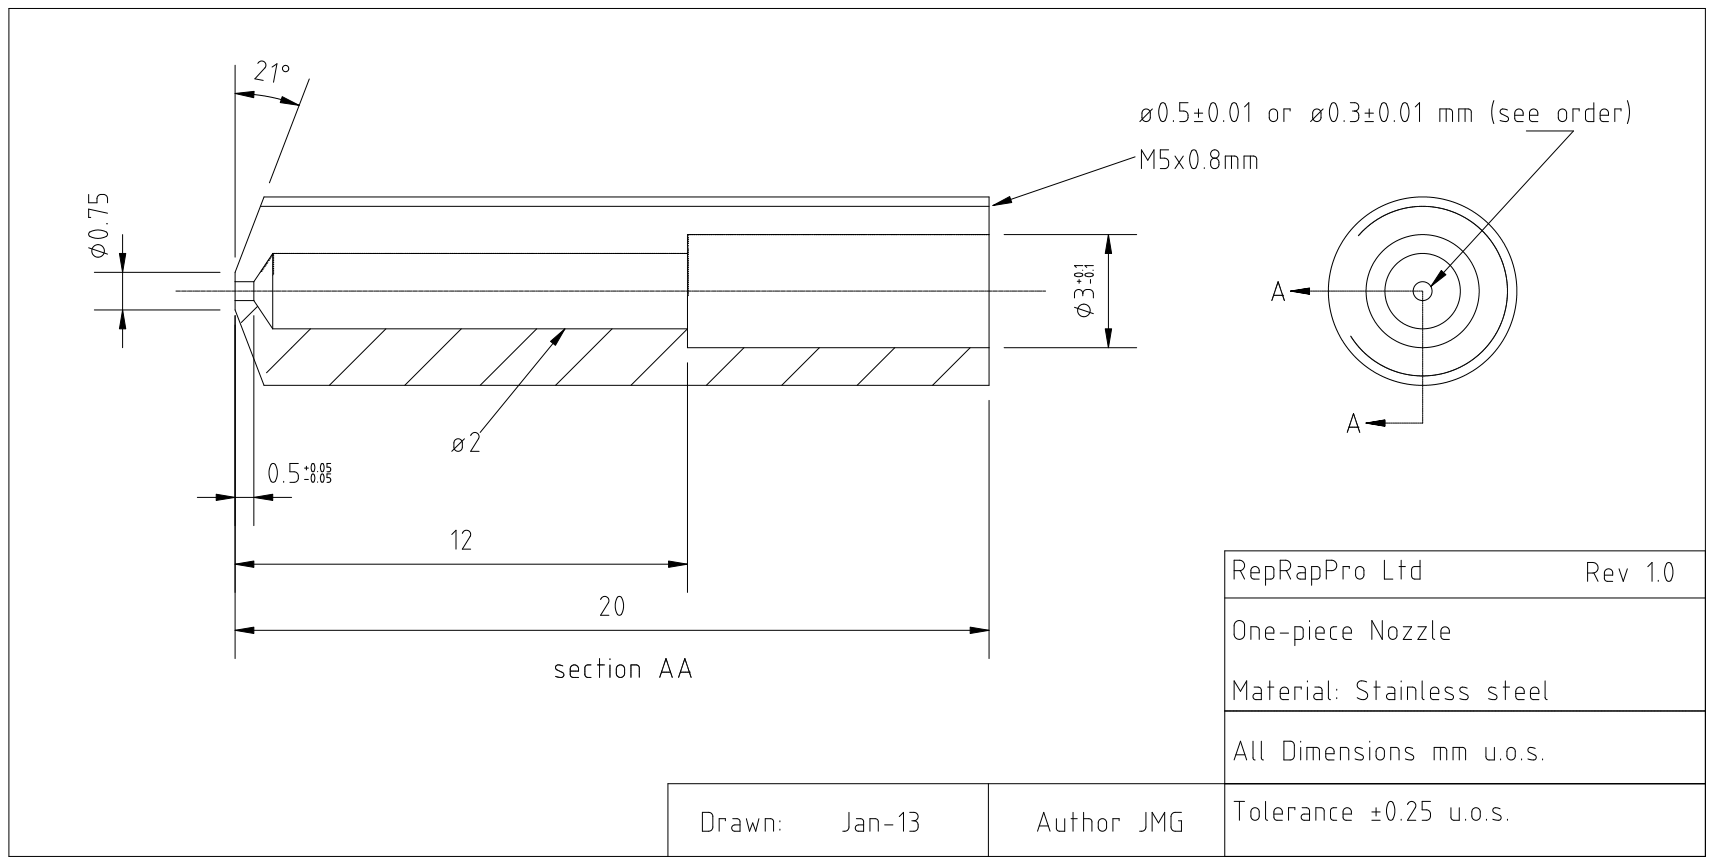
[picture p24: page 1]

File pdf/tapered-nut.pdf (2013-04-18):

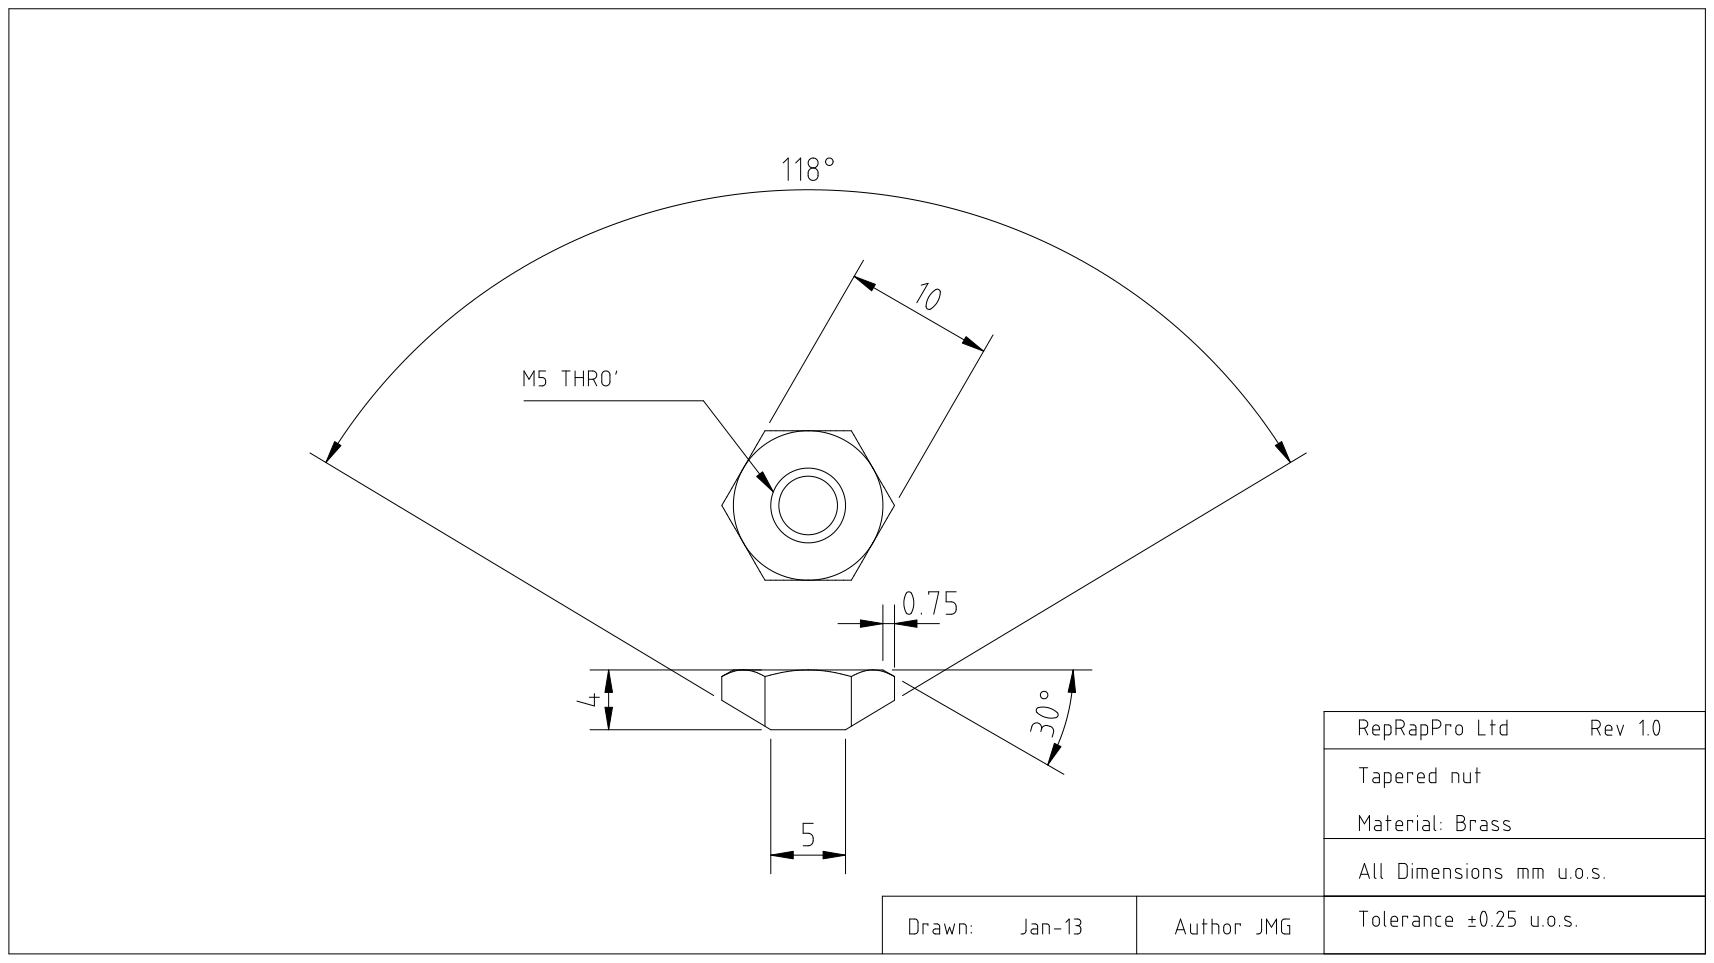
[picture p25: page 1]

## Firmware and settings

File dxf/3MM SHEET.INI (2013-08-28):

[Technics_Laser_Data]
ModifyTechCFG=0
LayersNumber=4
ExportRows=1
ExportColumns=1
ExportRowSpace=0.00000
ExportColumnSpace=0.00000
ExportRowCW=0.00000
ExportColumnCW=0.00000
LogicOrgPositionX=630.51235
LogicOrgPositionY=356.40314
LogicOrgPositionZ=-9999999.00000
AtOnceExport=1
IsTwoLaserWorking=0
TableZeroPositionX=0.00000
TableZeroPositionY=0.00000
OutputTimes=1
DelayTime=0
FeedLength=0.00000
FeedSpeed=5.00000
FeedDelayTime=0
MinX=36.08958
MaxX=630.51235
MinY=70.63552
MaxY=356.40314
ChangeSerialNo=0
ArrayMinX=36.08958
ArrayMaxX=630.51235
ArrayMinY=70.63552
ArrayMaxY=356.40314
ClipBoxPower=40.00000
ClipBoxPower2=40.00000
ClipBoxOffsetLen=2.00000
ClipBoxSpeed=25.00000
AlignMachineZPos=0.00000
RouteLength=0.00000
RoutePointNumber=0
OffsetLaserPower=0.00000
OffsetWorkSpeedPer=1.00000
ZHeightForLaserFocus=0.00000
LayerColor_0=0
LayerColor_1=255
LayerColor_2=1048455
LayerColor_3=10027161
OneWorkNeedTimes=0
TotalWorkTimes=0
[CoordSystem_0]
LogicOrgPosition1=630.51235
LogicOrgPosition2=356.40314
LogicOrgPosition3=-9999999.00000
SPLITBLOCK_NUMBER=2
SPLITBLOCK_NUMBER_0=0.00000
SPLITBLOCK_NUMBER_1=100000.00000
[CreateTechnicsCodeMgr]
PrjHasModifyCFG=1
[TechnicsLayers_0]
TechnicsMode=TECHNICS_LASERCUT
LaserCutConnerPower=100.00000
LaserCutWorkPower=100.00000
LaserCutConnerPower2=85.00000
LaserCutWorkPower2=90.00000
LaserCutFrequency=20000
LaserCutOptimizePathType=1
LaserCutInnerToOuter=1
LaserCutInnerToOuter2=0
LaserCutDownToUpper=0
LaserCutBlockHeight=150.00000
LaserCutAutoSetPathDir=0
LaserCutCicleMinSegNumber=36
LaserCutDisperseLength=0.02000
LaserCutCloseGapLength=0.05000
LaserCutOverlapLength=0.00000
LaserCutAdjustForClose=0
LaserCutQXEnterLength=0.00000
LaserCutDelayMoveTime=0.00000
LaserCutOpenGZDelayTime=0.00000
LaserCutOpenLaserDelayTime=0.00000
LaserCutCloseLaserDelayTime=0.00000
LaserCutDelayTimeAfterCloseLaser=0.00000
LaserCutOneAxisBackLashLength=0.00000
LaserCutTwoAxisBackLashLength=0.00000
LaserCutBackLashAddSpaceLength=8.00000
LaserCutBlowGasType=2
LaserCutAheadBlowGasTimes=0.00000
LaserCutNoCloseGasTimes=0.00000
LaserCutSpeed=12.00000
LaserCutGWAcc=80.00000
LaserCutGWTime=0.01000
LaserCutTrackSize=100
LaserCutLineLength=0.00000
SpaceCutLineLength=0.00000
bSpaceLineFirst=0
LaserCutAdjustMove=0
LaserCutAdjustMoveDelay=0.00000
LaserCutUpLen=0.00000
LaserCutCircleSpeedNum=0
TechnicsNeedOutput=0
GROUP_ROWS_0=1
GROUP_COLUMNS_0=1
GROUP_ROWSPACE_0=0.00000
GROUP_COLUMNSPACE_0=0.00000
GROUP_ROWCWSPACE_0=0.00000
GROUP_COLUMNCWSPACE_0=0.00000
GROUP_MINX_0=340.00606
GROUP_MAXX_0=340.00606
GROUP_MINY_0=114.05202
GROUP_MAXY_0=115.60757
[TechnicsLayers_1048455]
TechnicsMode=TECHNICS_LASERCUT
LaserCutConnerPower=65.00000
LaserCutWorkPower=65.00000
LaserCutConnerPower2=85.00000
LaserCutWorkPower2=90.00000
LaserCutFrequency=20000
LaserCutOptimizePathType=1
LaserCutInnerToOuter=1
LaserCutInnerToOuter2=0
LaserCutDownToUpper=0
LaserCutBlockHeight=150.00000
LaserCutAutoSetPathDir=0
LaserCutCicleMinSegNumber=36
LaserCutDisperseLength=0.02000
LaserCutCloseGapLength=0.05000
LaserCutOverlapLength=0.00000
LaserCutAdjustForClose=0
LaserCutQXEnterLength=0.00000
LaserCutDelayMoveTime=0.00000
LaserCutOpenGZDelayTime=0.00000
LaserCutOpenLaserDelayTime=0.00000
LaserCutCloseLaserDelayTime=0.00000
LaserCutDelayTimeAfterCloseLaser=0.00000
LaserCutOneAxisBackLashLength=0.00000
LaserCutTwoAxisBackLashLength=0.00000
LaserCutBackLashAddSpaceLength=8.00000
LaserCutBlowGasType=2
LaserCutAheadBlowGasTimes=0.00000
LaserCutNoCloseGasTimes=0.00000
LaserCutSpeed=15.00000
LaserCutGWAcc=80.00000
LaserCutGWTime=0.01000
LaserCutTrackSize=100
LaserCutLineLength=0.00000
SpaceCutLineLength=0.00000
bSpaceLineFirst=0
LaserCutAdjustMove=0
LaserCutAdjustMoveDelay=0.00000
LaserCutUpLen=0.00000
LaserCutCircleSpeedNum=0
GROUP_ROWS_0=1
GROUP_COLUMNS_0=1
GROUP_ROWSPACE_0=0.00000
GROUP_COLUMNSPACE_0=0.00000
GROUP_ROWCWSPACE_0=0.00000
GROUP_COLUMNCWSPACE_0=0.00000
GROUP_MINX_0=36.08958
GROUP_MAXX_0=630.51235
GROUP_MINY_0=70.63552
GROUP_MAXY_0=356.34275
[TechnicsLayers_8323072]
TechnicsMode=TECHNICS_LASERCUT
LaserCutConnerPower=100.00000
LaserCutWorkPower=100.00000
LaserCutConnerPower2=85.00000
LaserCutWorkPower2=90.00000
LaserCutFrequency=20000
LaserCutOptimizePathType=1
LaserCutInnerToOuter=1
LaserCutInnerToOuter2=0
LaserCutDownToUpper=0
LaserCutBlockHeight=150.00000
LaserCutAutoSetPathDir=0
LaserCutCicleMinSegNumber=36
LaserCutDisperseLength=0.02000
LaserCutCloseGapLength=0.05000
LaserCutOverlapLength=0.00000
LaserCutAdjustForClose=0
LaserCutQXEnterLength=0.00000
LaserCutDelayMoveTime=0.00000
LaserCutOpenGZDelayTime=0.00000
LaserCutOpenLaserDelayTime=0.00000
LaserCutCloseLaserDelayTime=0.00000
LaserCutDelayTimeAfterCloseLaser=0.00000
LaserCutOneAxisBackLashLength=0.00000
LaserCutTwoAxisBackLashLength=0.00000
LaserCutBackLashAddSpaceLength=8.00000
LaserCutBlowGasType=2
LaserCutAheadBlowGasTimes=0.00000
LaserCutNoCloseGasTimes=0.00000
LaserCutSpeed=400.00000
LaserCutGWAcc=80.00000
LaserCutGWTime=0.01000
LaserCutTrackSize=100
LaserCutLineLength=0.00000
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

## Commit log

2012-02-09 Setting up Prusa Mendel
    [configuration.scad, endstop-holder-3off.scad, gregs-x-carriage-1off.scad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]
2012-02-09 More work on the Prusa OpenSCAD files.
    [bar-clamp-8off.scad, belt-clamp-readme.scad, configuration.scad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]
2012-02-12 Further work on the Prusa design...
    [bearing-mount-include.scad, endstop-holder-readme.scad, frame-vertex-2off.stl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]
2012-02-21 3-head X carriage designed.
    [bearing-mount-include.scad, belt-clamp-readme.scad, frame-vertex-2off.stl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]
2012-02-21 Expanded x-rod gap to accommodate multipe extruders.
    [bearing-mount-include.scad, configuration.scad, x-carriage-1off.scad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]
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2012-02-23 Improved designs of bearing holder and X carriage
    [bearing-mount-include.scad, x-carriage-lid-1off.stl, x-carriage-plate-1off.stl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]
2012-02-25 Added design for Y frog. Modified X ends to resist movement under belt tension.
    [frame-vertex-foot-4off.stl, frame-vertex-readme.scad, x-end-idler-1off.stl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]
2012-02-25 Improved design of Y frog so it can be lasered or printed.
    [heatbed.sch, y-frog.dxf]
2012-03-01 Further design tidying. X carriage inverted.
    [belt-clamp-readme.scad, configuration.scad, x-belt-clamp-2off.stl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]
2012-03-04 Draft design for heatbed insulator added - will need to be modified for finel PCB.
    [bearing-mount-include.scad, heatbed-insulator.dxf]
2012-03-09 Setting up the RFO print files.
    [bar-clamp-8off.stl, belt-clamp-readme.scad, configuration.scad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]
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2012-03-19 Wiring entries added to Mendel BoM
    [RepRapPro-Mendel-BoM.ods]
2012-03-20 Added tounge and idler scads.
    [idler.scad, idler.stl, tongue.scad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]
2012-03-21 BoM complete (maybe...). Modified design of heated bed lasercut insulator.
    [RepRapPro-Mendel-BoM.ods, extruder-drive-mount-1off.scad, extruder-drive-mount-1off.stl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]
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2012-03-28 Better design of heated bed insulator.
    [bar-clamp-8off.scad, bar-clamp-8off.stl, heatbed-insulator.dxf]
2012-03-29 Endstop tab and hotend PCB mount added to X carriage.
    [hot-end-pcb-bracket-1off.scad, hot-end-pcb-bracket-1off.stl, x-carriage-plate-1off.stl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]
2012-03-29 Improved heated bed insulator.
    [heatbed-insulator.dxf]
2012-04-01 Various minor corrections and upgrades.
    [Tray-1.scad, Tray-3.scad, aluminium-heat-spreader.dxf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]
2012-04-03 Increased stiffness of Y frog.
    [y-frog.dxf]
2012-04-04 Design of Al heatspreader finished.
    [aluminium-heat-spreader.dxf, heatbed-insulator.dxf]
2012-04-04 DXF for heatshield added.
    [cardboard-heat-shield.dxf, x-carriage-readme.scad]
2012-04-08 Added ZIP file of all the Mendel STLs.
    [idler-dont-print-me.stl, idler.scad, tongue-1off.stl]
2012-04-10 Improved design of Y motor mount.
    [ps-cover-1off.scad, y-motor-mount-plate-1off.stl, y-motor-mount-readme.scad]
2012-04-17 Start design of power supply cover.
    [ps-cover-1off.scad]
2012-04-22 Improved design of X carriage ends.
    [bearing-mount-include.scad, idler.stl, ps-cover-1off.scad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]
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2012-05-10 Extra cable tie holes added to bed insulator.
    [heatbed-insulator.dxf]
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2012-05-29 Minor improvement to the Z motor mount design.
    [configuration.scad, z-motor-mount-2off.scad, z-motor-mount-2off.stl]
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2012-07-05 Moved a few files to make nanes consistent.
    [ps-cover-x2.stl, ps-cover-x2_stl.scad, pulley-14tooth.stl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]
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2012-07-14 Minor design improvements to printed parts - Better M3 holes on Y motor brackets No un-needed holes on X motor mount Hex cavities moved to topside of Y bearing mounts for easier bed adjustment
    [bearing-mount-include.scad, x-end-motor-1off.stl, x-end-readme.scad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]
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2012-10-17 changes to heatbed shield and heat spreader to accommodate new heatbed connection design
    [aluminium-heat-spreader.dxf, heatbed-insulator.dxf]
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2012-11-25 most sizes tweaked. x ends igus needs 0.1mm more on dia.
    [3587.stl, 3587_stl.scad, 4042.stl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]
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2012-11-26 Getting extruder drive design files in the right place.
    [extruder-drive-retaining-block.stl, extruder-drive.scad]
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2013-01-25 Uploading redesigned x carriage
    [X-Axis.SLDASM, nozzle-mount-front.SLDPRT, nozzle-mount-rear.SLDPRT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]
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2013-01-26 Tweaking Y motor bracket for production, Almost finished!!!!!
    [Y-Motor-Bracket.DXF]
2013-01-26 Updating PCB heatbed DXF to be symmetric to ease assembly and do include marking for heatbed polarity
    [heatbed-insulator.DXF]
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2013-01-31 Tweaking Endstop holder snap fit and renaming files
    [EndStop-Holder.SLDPRT, EndStop-Holder_2off.STL, Y-Bearing-Holder_1off.STL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]
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2013-02-04 Further updates to X carriage to minimise heat warp from multiple extruders
    [nozzle-mount-front.SLDPRT, nozzle-mount-front_1off.STL, nozzle-mount-rear.SLDPRT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]
2013-02-05 Further X carriage updates to minimise heat warp
    [nozzle-mount-front.SLDPRT, nozzle-mount-rear.SLDPRT, x-carriage.SLDPRT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]
2013-02-05 Further tweaking of X carriage and Nozzle mounts
    Extended testing conducted @240degrees extruder, 110 degree bed with
    PLA parts. No failure observed with final design with no heat
    reflector, even in worse case scenario holding the nozzle directly
    above the bed for extended periods. Failure eventually resulted from
    failure of bottom linear bearing seal degrading resulting inconsistent
    motion.
    [nozzle-mount-front.SLDPRT, nozzle-mount-rear.SLDPRT, x-carriage.SLDPRT]
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2013-02-09 Adding chamfers to bottom surfaces to reduce effect of lip during printing
    [x-end-idler.SLDPRT, x-end-motor.SLDPRT, x-idler-cover.SLDPRT]
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2013-04-22 Simple test part from documentation added to multi-colour test parts.
    [green.stl, red.stl, simple-test.scad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]
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2013-05-29 Organising the Individual-STLs folder to make it easier for people to print.
    [Fan Holder.STL, FanMount.STL, belt-guide-4off.stl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]
2013-05-29 Y-motor-mount added as STL if people want to print it rather than lasering it.
    [bar-clamp-1off.g, bar-clamp-1off_.g, optional-y-motor-mount-2off.stl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]
2013-05-29 Y-Frog added as STLs. The OpenSCAD that generates them from the laser DXF file is in the OpenSCAD directory.
    [optional-y-frog-A-1off.stl, optional-y-frog-B-1off.stl, y-frog-1off.scad]
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2013-06-07 New trays laid out that should print a little better.
    [tray1-new.stl, tray1.stl, tray2-new.stl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]
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
